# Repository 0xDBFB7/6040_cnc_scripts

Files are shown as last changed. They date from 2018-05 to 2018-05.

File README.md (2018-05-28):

This documents my continuing mission to make 6040 cncs usable.

This contains LinuxCNC configs, python-EMC2 utilities (hole probing, etc.), a threadmill program generator, etc.

It assumes that you have limit switches on all axis, all of which are connected in parallel to one of the inputs. If your CNC doesn't have the input pins broken out, you can buy a 5-position JST-XH 2.5mm plug and connect it to the parallel port breakout:

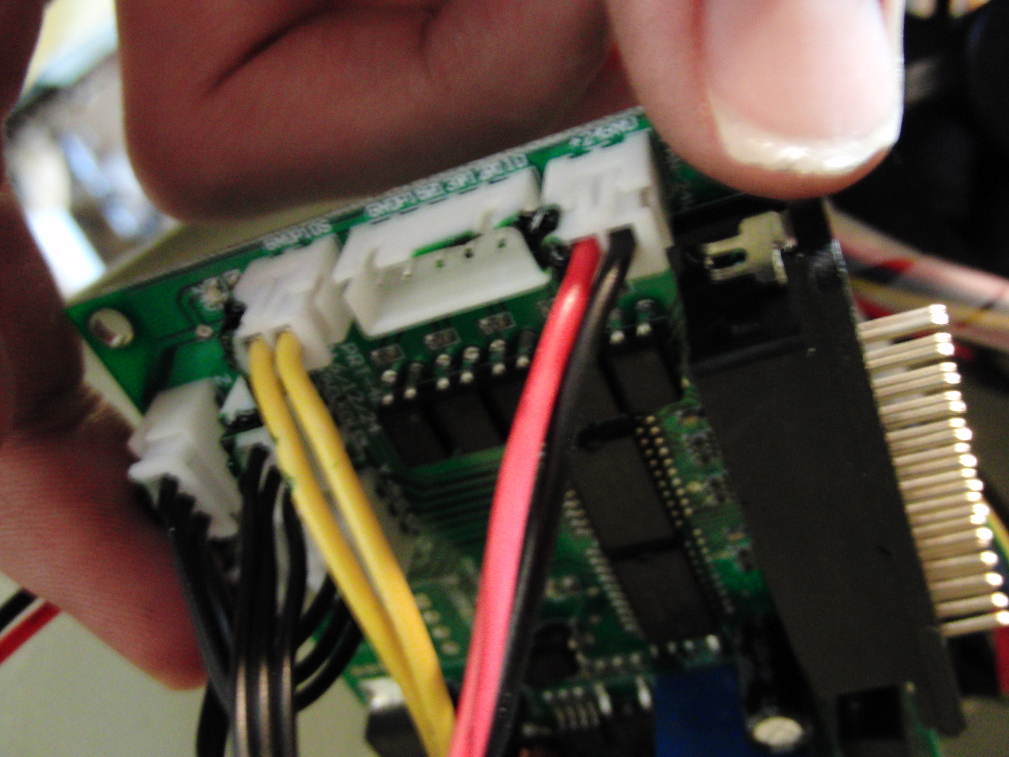
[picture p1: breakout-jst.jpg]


I spent a while looking for a touch probe system to use on these machines, but I couldn't really find anything that suited my needs. All the homemade stuff generally has concentricity issues etc. 

I found this 1/4" shaft from McMaster that has a 0.002" ceramic coating on it - it's under "Linear Motion Shafts for Harsh Environments", part number 1031K61. If you lathe off 2cm of the coating from one end, and chuck the insulated end in the spindle, you get a totally workable touch probe:

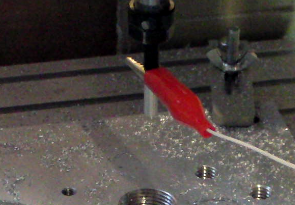
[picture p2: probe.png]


I've gotten repeatability values of around 0.05mm with this setup. 

I also recommend you get a cheap tool touch plate from eBay - they're like $5. I wired the touch plate and an alligator clip for the probe to the LinuxCNC probe input - just make sure you ground the probe itself if you're touching off:

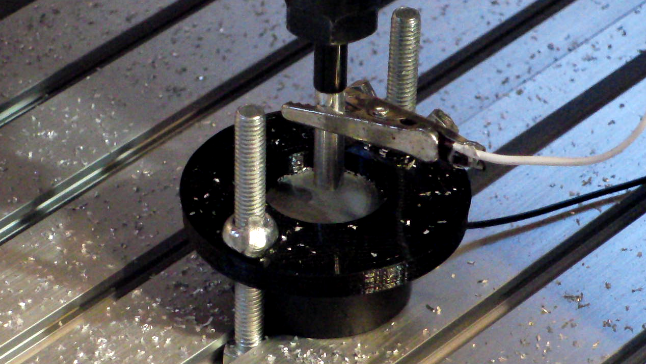
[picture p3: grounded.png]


I'm using a rather convoluted method for tool height adjustment, though it does function.

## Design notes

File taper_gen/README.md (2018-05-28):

This is a thread mill program generator for SPTM mills. It can produce nearly any type of thread, including NPT tapered. Just install python, input the desired values, and run.

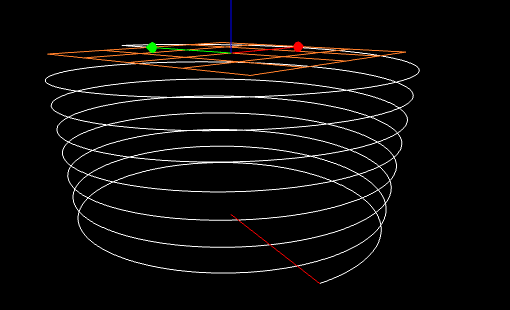
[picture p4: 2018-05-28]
taper_gen/taper.png

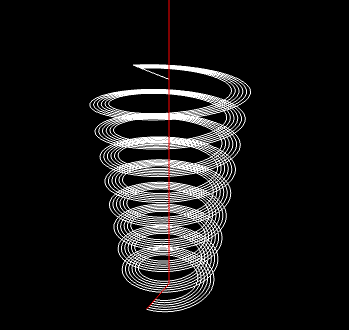
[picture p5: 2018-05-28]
taper_gen/taper2.png

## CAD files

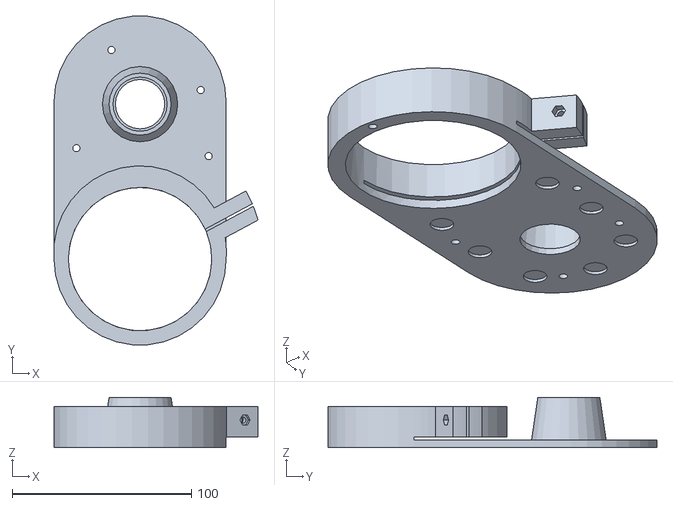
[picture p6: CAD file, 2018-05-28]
hardware/dusfinal (1).stl
113.8 x 183.2 x 28.0

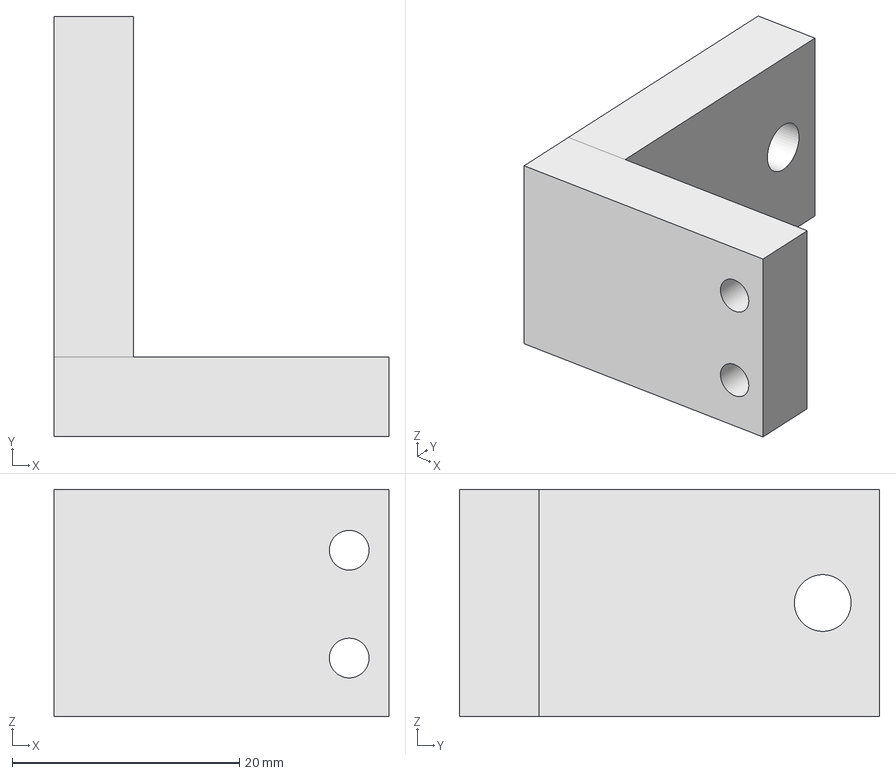
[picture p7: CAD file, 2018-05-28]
hardware/cnc_limit_1.fcstd
29.5 x 37.0 x 20.0 mm

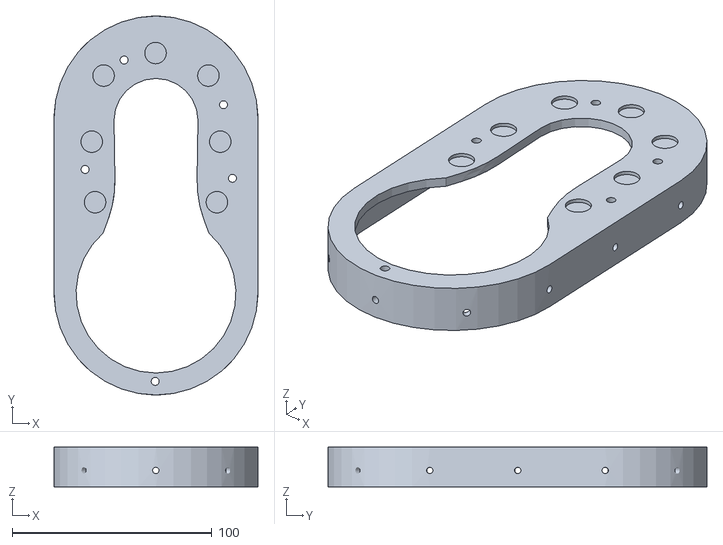
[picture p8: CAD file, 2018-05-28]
hardware/dusfina2l (1).stl
102.0 x 189.6 x 20.0

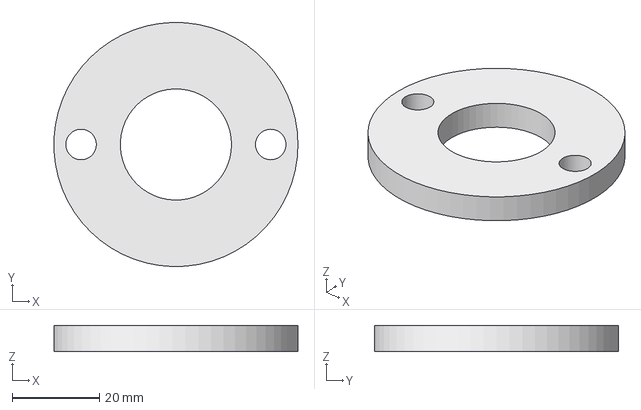
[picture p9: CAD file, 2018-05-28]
hardware/cnc_z_holder.fcstd
56.0 x 56.0 x 6.00 mm

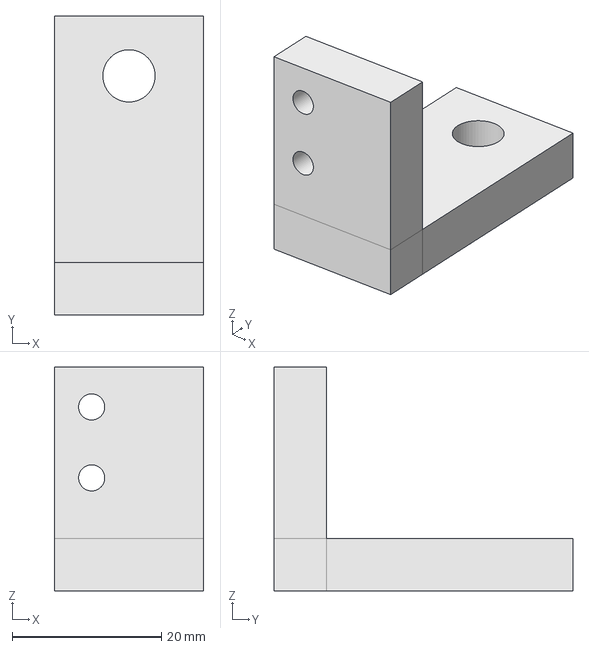
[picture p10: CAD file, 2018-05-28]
hardware/cnc_limit_2.fcstd
20.0 x 40.0 x 30.0 mm

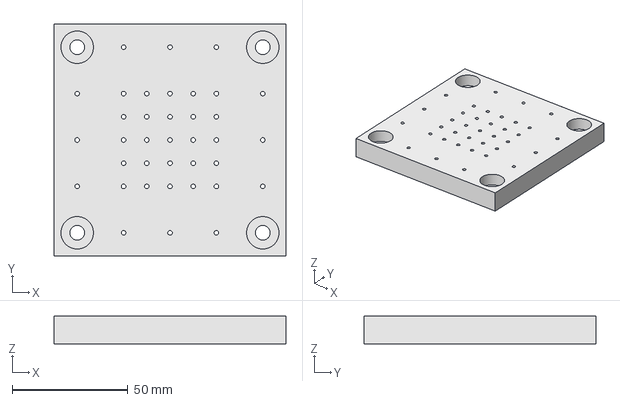
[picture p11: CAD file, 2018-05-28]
hardware/grid_plate.fcstd
100.0 x 100.0 x 11.9 mm

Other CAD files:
hardware/grid_plate.stl

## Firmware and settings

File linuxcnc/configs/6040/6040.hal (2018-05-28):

# Generated by stepconf 1.1 at Sat Dec 16 13:42:40 2017
# If you make changes to this file, they will be
# overwritten when you run stepconf again
loadrt trivkins
loadrt [EMCMOT]EMCMOT base_period_nsec=[EMCMOT]BASE_PERIOD servo_period_nsec=[EMCMOT]SERVO_PERIOD num_joints=[TRAJ]AXES
loadrt hal_parport cfg="0 out"
setp parport.0.reset-time 5000
loadrt stepgen step_type=0,0,0,0
loadrt pwmgen output_type=1

addf parport.0.read base-thread
addf stepgen.make-pulses base-thread
addf pwmgen.make-pulses base-thread
addf parport.0.write base-thread
addf parport.0.reset base-thread

addf stepgen.capture-position servo-thread
addf motion-command-handler servo-thread
addf motion-controller servo-thread
addf stepgen.update-freq servo-thread
addf pwmgen.update servo-thread

net spindle-cmd-rpm => pwmgen.0.value
net spindle-on <= motion.spindle-on => pwmgen.0.enable
net spindle-pwm <= pwmgen.0.pwm
setp pwmgen.0.pwm-freq 301.0
setp pwmgen.0.scale 29375.0
setp pwmgen.0.offset 0.182978723404
setp pwmgen.0.dither-pwm true
net spindle-cmd-rpm     <= motion.spindle-speed-out
net spindle-cmd-rpm-abs <= motion.spindle-speed-out-abs
net spindle-cmd-rps     <= motion.spindle-speed-out-rps
net spindle-cmd-rps-abs <= motion.spindle-speed-out-rps-abs
net spindle-at-speed    => motion.spindle-at-speed
net spindle-cw <= motion.spindle-forward

net probe-in => motion.probe-input
net din-01 => motion.digital-in-01
net din-02 => motion.digital-in-02

setp parport.0.pin-01-out-invert 1
net spindle-pwm     => parport.0.pin-01-out
net xstep           => parport.0.pin-02-out
setp parport.0.pin-02-out-reset 1
net xdir            => parport.0.pin-03-out
net ystep           => parport.0.pin-04-out
setp parport.0.pin-04-out-reset 1
net ydir            => parport.0.pin-05-out
net zstep           => parport.0.pin-06-out
setp parport.0.pin-06-out-reset 1
net zdir            => parport.0.pin-07-out
net astep           => parport.0.pin-08-out
setp parport.0.pin-08-out-reset 1
net adir            => parport.0.pin-09-out
setp parport.0.pin-14-out-invert 1
net spindle-on      => parport.0.pin-14-out
setp parport.0.pin-17-out-invert 1
net spindle-cw      => parport.0.pin-17-out
net estop-ext       <= parport.0.pin-10-in
net probe-in        <= parport.0.pin-11-in
net din-01          <= parport.0.pin-12-in
net din-02          <= parport.0.pin-13-in
net all-home        <= parport.0.pin-15-in

setp stepgen.0.position-scale [AXIS_0]SCALE
setp stepgen.0.steplen 1
setp stepgen.0.stepspace 0
setp stepgen.0.dirhold 35000
setp stepgen.0.dirsetup 35000
setp stepgen.0.maxaccel [AXIS_0]STEPGEN_MAXACCEL
net xpos-cmd axis.0.motor-pos-cmd => stepgen.0.position-cmd
net xpos-fb stepgen.0.position-fb => axis.0.motor-pos-fb
net xstep <= stepgen.0.step
net xdir <= stepgen.0.dir
net xenable axis.0.amp-enable-out => stepgen.0.enable
net all-home => axis.0.home-sw-in

setp stepgen.1.position-scale [AXIS_1]SCALE
setp stepgen.1.steplen 1
setp stepgen.1.stepspace 0
setp stepgen.1.dirhold 35000
setp stepgen.1.dirsetup 35000
setp stepgen.1.maxaccel [AXIS_1]STEPGEN_MAXACCEL
net ypos-cmd axis.1.motor-pos-cmd => stepgen.1.position-cmd
net ypos-fb stepgen.1.position-fb => axis.1.motor-pos-fb
net ystep <= stepgen.1.step
net ydir <= stepgen.1.dir
net yenable axis.1.amp-enable-out => stepgen.1.enable
net all-home => axis.1.home-sw-in

setp stepgen.2.position-scale [AXIS_2]SCALE
setp stepgen.2.steplen 1
setp stepgen.2.stepspace 0
setp stepgen.2.dirhold 35000
setp stepgen.2.dirsetup 35000
setp stepgen.2.maxaccel [AXIS_2]STEPGEN_MAXACCEL
net zpos-cmd axis.2.motor-pos-cmd => stepgen.2.position-cmd
net zpos-fb stepgen.2.position-fb => axis.2.motor-pos-fb
net zstep <= stepgen.2.step
net zdir <= stepgen.2.dir
net zenable axis.2.amp-enable-out => stepgen.2.enable
net all-home => axis.2.home-sw-in

setp stepgen.3.position-scale [AXIS_3]SCALE
setp stepgen.3.steplen 1
setp stepgen.3.stepspace 0
setp stepgen.3.dirhold 35000
setp stepgen.3.dirsetup 35000
setp stepgen.3.maxaccel [AXIS_3]STEPGEN_MAXACCEL
net apos-cmd axis.3.motor-pos-cmd => stepgen.3.position-cmd
net apos-fb stepgen.3.position-fb => axis.3.motor-pos-fb
net astep <= stepgen.3.step
net adir <= stepgen.3.dir
net aenable axis.3.amp-enable-out => stepgen.3.enable
net all-home => axis.3.home-sw-in

net estop-out <= iocontrol.0.user-enable-out
net estop-ext => iocontrol.0.emc-enable-in

loadusr -W hal_manualtoolchange
net tool-change iocontrol.0.tool-change => hal_manualtoolchange.change
net tool-changed iocontrol.0.tool-changed <= hal_manualtoolchange.changed
net tool-number iocontrol.0.tool-prep-number => hal_manualtoolchange.number
net tool-prepare-loopback iocontrol.0.tool-prepare => iocontrol.0.tool-prepared

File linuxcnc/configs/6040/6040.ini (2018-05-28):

# Generated by stepconf 1.1 at Fri Dec 15 22:44:33 2017
# If you make changes to this file, they will be
# overwritten when you run stepconf again

[EMC]
MACHINE = 6040
DEBUG = 0

[DISPLAY]
DISPLAY = axis
EDITOR = gedit
POSITION_OFFSET = RELATIVE
POSITION_FEEDBACK = ACTUAL
ARCDIVISION = 64
GRIDS = 10mm 20mm 50mm 100mm 1in 2in 5in 10in
MAX_FEED_OVERRIDE = 1.2
MIN_SPINDLE_OVERRIDE = 0.5
MAX_SPINDLE_OVERRIDE = 1.2
DEFAULT_LINEAR_VELOCITY = 2.50
MIN_LINEAR_VELOCITY = 0
MAX_LINEAR_VELOCITY = 60.00
DEFAULT_ANGULAR_VELOCITY = 36.00
MIN_ANGULAR_VELOCITY = 0
MAX_ANGULAR_VELOCITY = 360.00
INTRO_GRAPHIC = linuxcnc.gif
INTRO_TIME = 5
PROGRAM_PREFIX = /home/cnc/linuxcnc/nc_files
INCREMENTS = 5mm 1mm .5mm .1mm .05mm .01mm .005mm

[FILTER]
PROGRAM_EXTENSION = .png,.gif,.jpg Greyscale Depth Image
PROGRAM_EXTENSION = .py Python Script
png = image-to-gcode
gif = image-to-gcode
jpg = image-to-gcode
py = python

[TASK]
TASK = milltask
CYCLE_TIME = 0.010

[RS274NGC]
PARAMETER_FILE = linuxcnc.var
TOLERANCE_INCH = 0.0005
TOLERANCE_MM = 0.0127

[EMCMOT]
EMCMOT = motmod
COMM_TIMEOUT = 1.0
COMM_WAIT = 0.010
BASE_PERIOD = 50000
SERVO_PERIOD = 1000000

[HAL]
HALFILE = 6040.hal
HALFILE = custom.hal
POSTGUI_HALFILE = custom_postgui.hal

[TRAJ]
AXES = 4
COORDINATES = X Y Z A
LINEAR_UNITS = mm
ANGULAR_UNITS = degree
CYCLE_TIME = 0.010
DEFAULT_VELOCITY = 36.00
MAX_VELOCITY = 25.00

[EMCIO]
EMCIO = io
CYCLE_TIME = 0.100
TOOL_TABLE = tool.tbl

[AXIS_0]
TYPE = LINEAR
HOME = 4.0
MAX_VELOCITY = 60.0
MAX_ACCELERATION = 400.0
STEPGEN_MAXACCEL = 500.0
SCALE = -320.0
FERROR = 1
MIN_FERROR = 0.25
MIN_LIMIT = 3.999
MAX_LIMIT = 349.0
HOME_OFFSET = 3.000000
HOME_SEARCH_VEL = 1.50000
HOME_LATCH_VEL = 0.200000
HOME_SEQUENCE = 1

[AXIS_1]
TYPE = LINEAR
HOME = 4.0
MAX_VELOCITY = 60.0
MAX_ACCELERATION = 400.0
STEPGEN_MAXACCEL = 500.0
SCALE = -320.0
FERROR = 1
MIN_FERROR = 0.25
MIN_LIMIT = 3.999
MAX_LIMIT = 549.0
HOME_OFFSET = 3.000000
HOME_SEARCH_VEL = 2.000000
HOME_LATCH_VEL = 0.200000
HOME_SEQUENCE = 2

[AXIS_2]
TYPE = LINEAR
HOME = 248.0
MAX_VELOCITY = 40
MAX_ACCELERATION = 400.0
STEPGEN_MAXACCEL = 500.0
SCALE = 400.0
FERROR = 1
MIN_FERROR = .25
MIN_LIMIT = -0.0
MAX_LIMIT = 249.0
HOME_OFFSET = 250.000000
HOME_SEARCH_VEL = -2.00000
HOME_LATCH_VEL = 0.20000
HOME_SEQUENCE = 0

[AXIS_3]
TYPE = ANGULAR
HOME = 0.0
MAX_VELOCITY = 360.0
MAX_ACCELERATION = 1200.0
STEPGEN_MAXACCEL = 1500.0
SCALE = 10.0
FERROR = 1
MIN_FERROR = .25
MIN_LIMIT = -9999.0
MAX_LIMIT = 9999.0
HOME_SEARCH_VEL = 0
HOME_LATCH_VEL = 0
HOME_SEQUENCE = 0
HOME_USE_INDEX = NO
